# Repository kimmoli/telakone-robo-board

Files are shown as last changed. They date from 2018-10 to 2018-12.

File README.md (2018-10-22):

# telakone-robo-board

## Requirements

* Input power supply range 12..50V
* 5V regulator for external stuff (servos, LEDs, ...)
* CPU STM32F407
* RS-485 half-duplex serial interface
* PS2 (playstation) control (SPI)
  * SPI1
    * SPI1_SCK PB3 AF5
    * SPI1_MISO PB4 AF5
    * SPI1_MOSI PB5 AF5
    * SPI_CS_N PA8 OUTPUT
* I2C for external acceleration sensors
  * I2C1
    * I2C1_SCL PB6 AF4
    * I2C1_SDA PB7 AF4
* WS2812B control for LED lights
  * USART2
    * USART2_TX PA2
* USB device interface
  * Virtual serial port
    * OTG_FS_DM PA11 AF10
    * OTG_FS_DP PA12 AF10
	* USB_RENUM PB15 OUTPUT
* Wired UART
  * USART3
    * USART3_TX PD8 AF7
    * USART3_RX PD9 AF7
* RS485 UART
  * USART1
    * USART1_TX PA9 AF7
	* USART1_RX PA10 AF7
	* USART1_TXE PD15 OUTPUT
* Digital outputs
  * 1 enable output for stepper drivers
    * PE14 OUTPUT
  * 6 frequency outputs for stepper drivers
    * TIM4_CH1 PD12 AF2
    * TIM5_CH1 PA0 AF2
    * TIM8_CH1 PC6 AF3
    * TIM9_CH1 PE5 AF3
    * TIM10_CH1 PB8 AF3
    * TIM11_CH1 PB9 AF3
  * 6 direction outputs for stepper drivers
    * PE8 OUTPUT
    * PE9 OUTPUT
    * PE10 OUTPUT
    * PE11 OUTPUT
    * PE12 OUTPUT
    * PE13 OUTPUT
  * 2 servo signal outputs
    * TIM3_CH1 PA6 AF2
    * TIM3_CH2 PA7 AF2
  * 2 high side switch outputs
    * PC0 OUTPUT
    * PC1 OUTPUT
  * 3 debug led outputs
    * PC2 OUTPUT DEBUG (Green)
	* PC3 OUTPUT RUN (Green)
	* PC4 OUTPUT ERROR (Red)
* Digital inputs
  * 16 inputs for limit/zero switches, emergency stop
    * PC8 INPUT
    * PC9 INPUT
    * PC10 INPUT
    * PC11 INPUT
    * PC12 INPUT
    * PC13 INPUT
    * PC14 INPUT
    * PC15 INPUT
    * PD0 INPUT
    * PD1 INPUT
    * PD2 INPUT
    * PD3 INPUT
    * PD4 INPUT
    * PD5 INPUT
    * PD6 INPUT
    * PD7 INPUT

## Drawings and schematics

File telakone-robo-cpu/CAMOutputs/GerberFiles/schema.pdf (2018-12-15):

+5V 3A

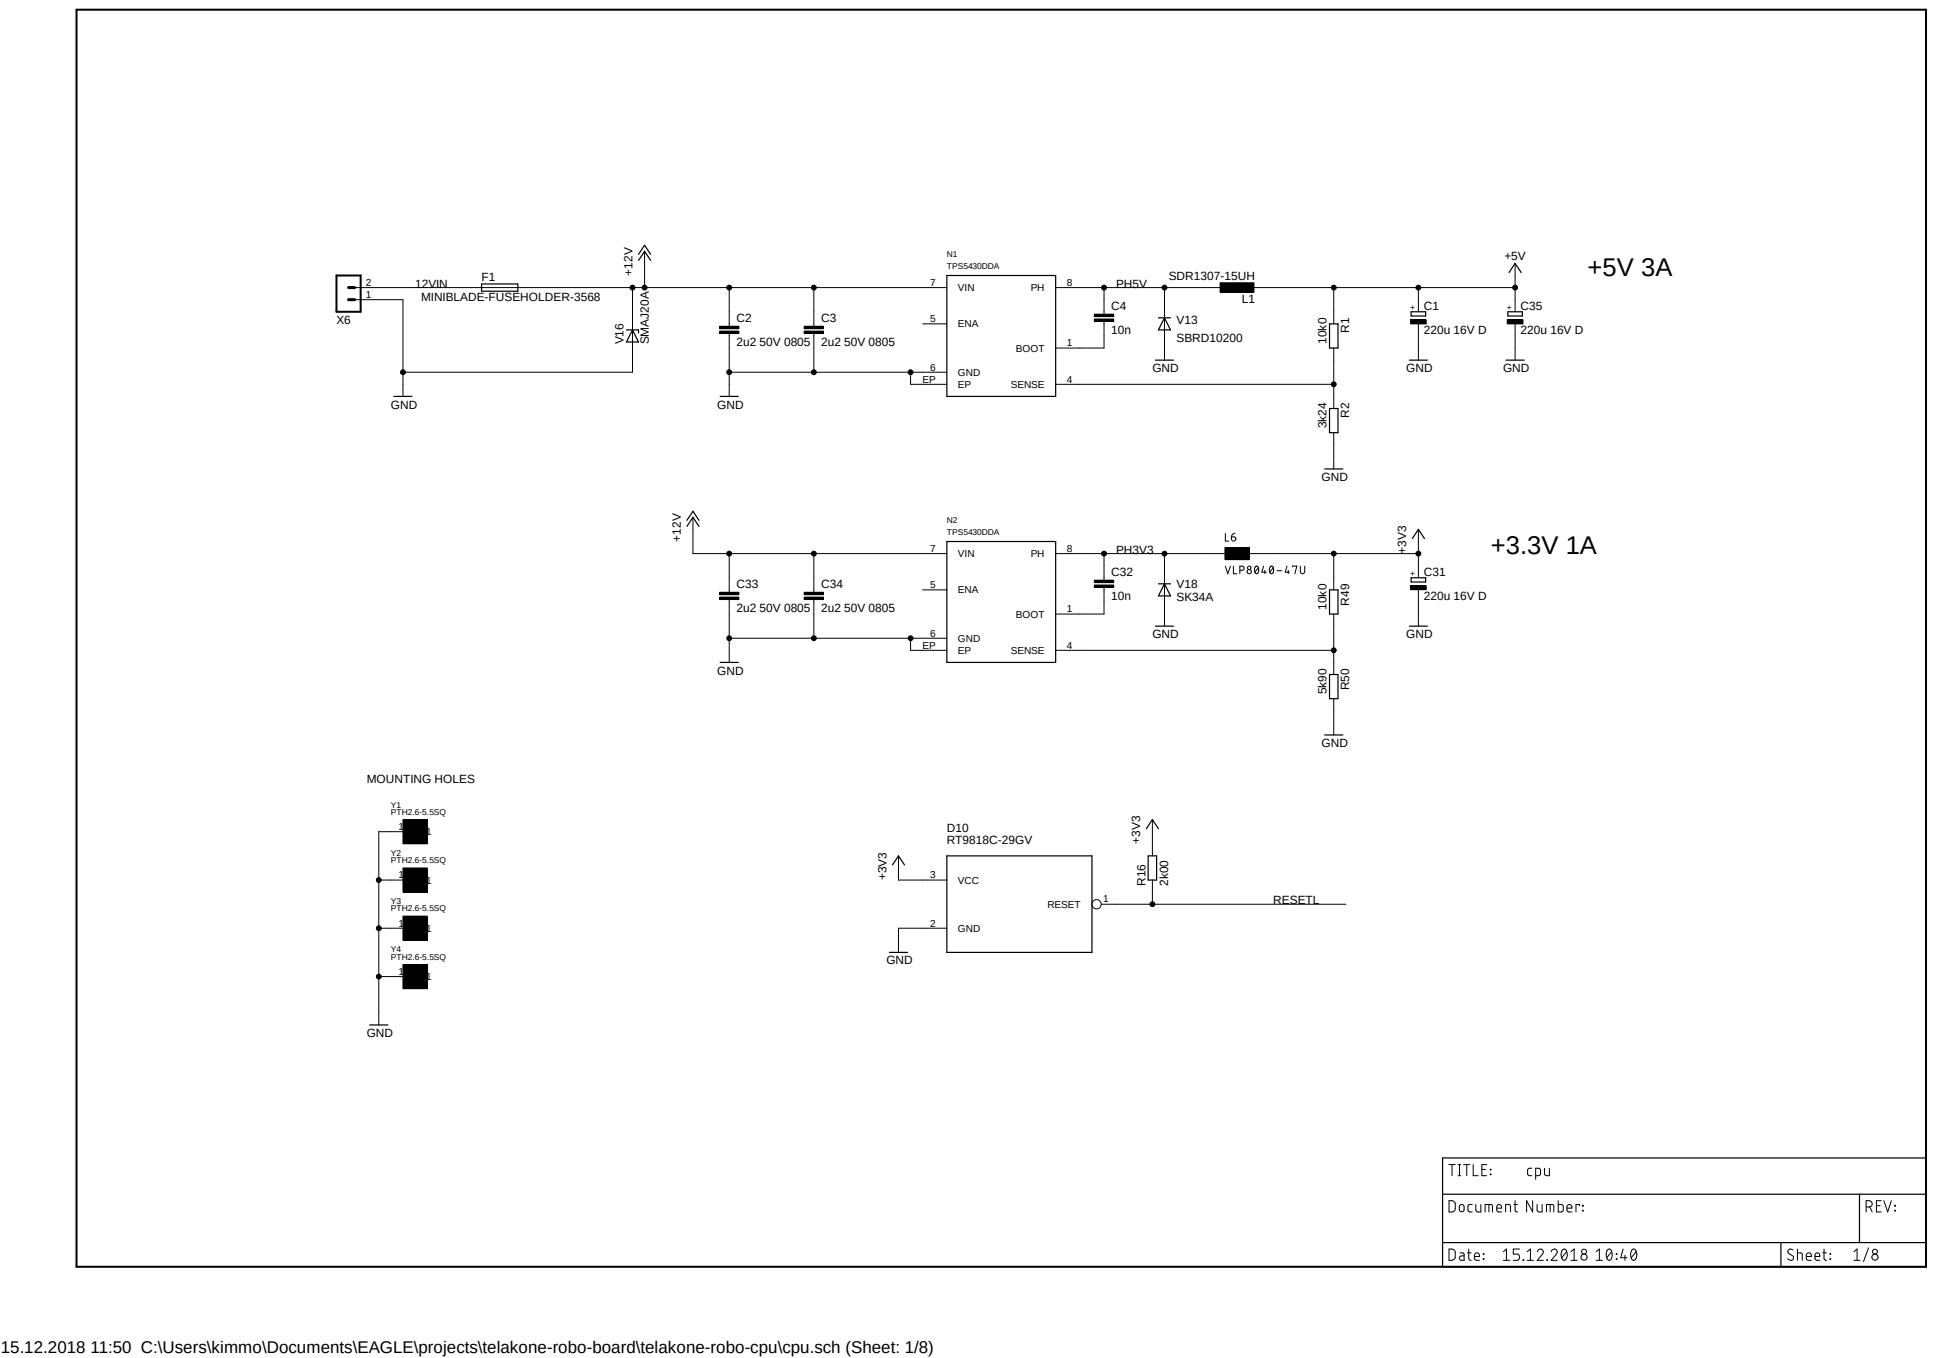
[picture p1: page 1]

15.12.2018 11:50 C:\Users\kimmo\Documents\EAGLE\projects\telakone-robo-board\telakone-robo-cpu\cpu.sch (Sheet: 1/8)

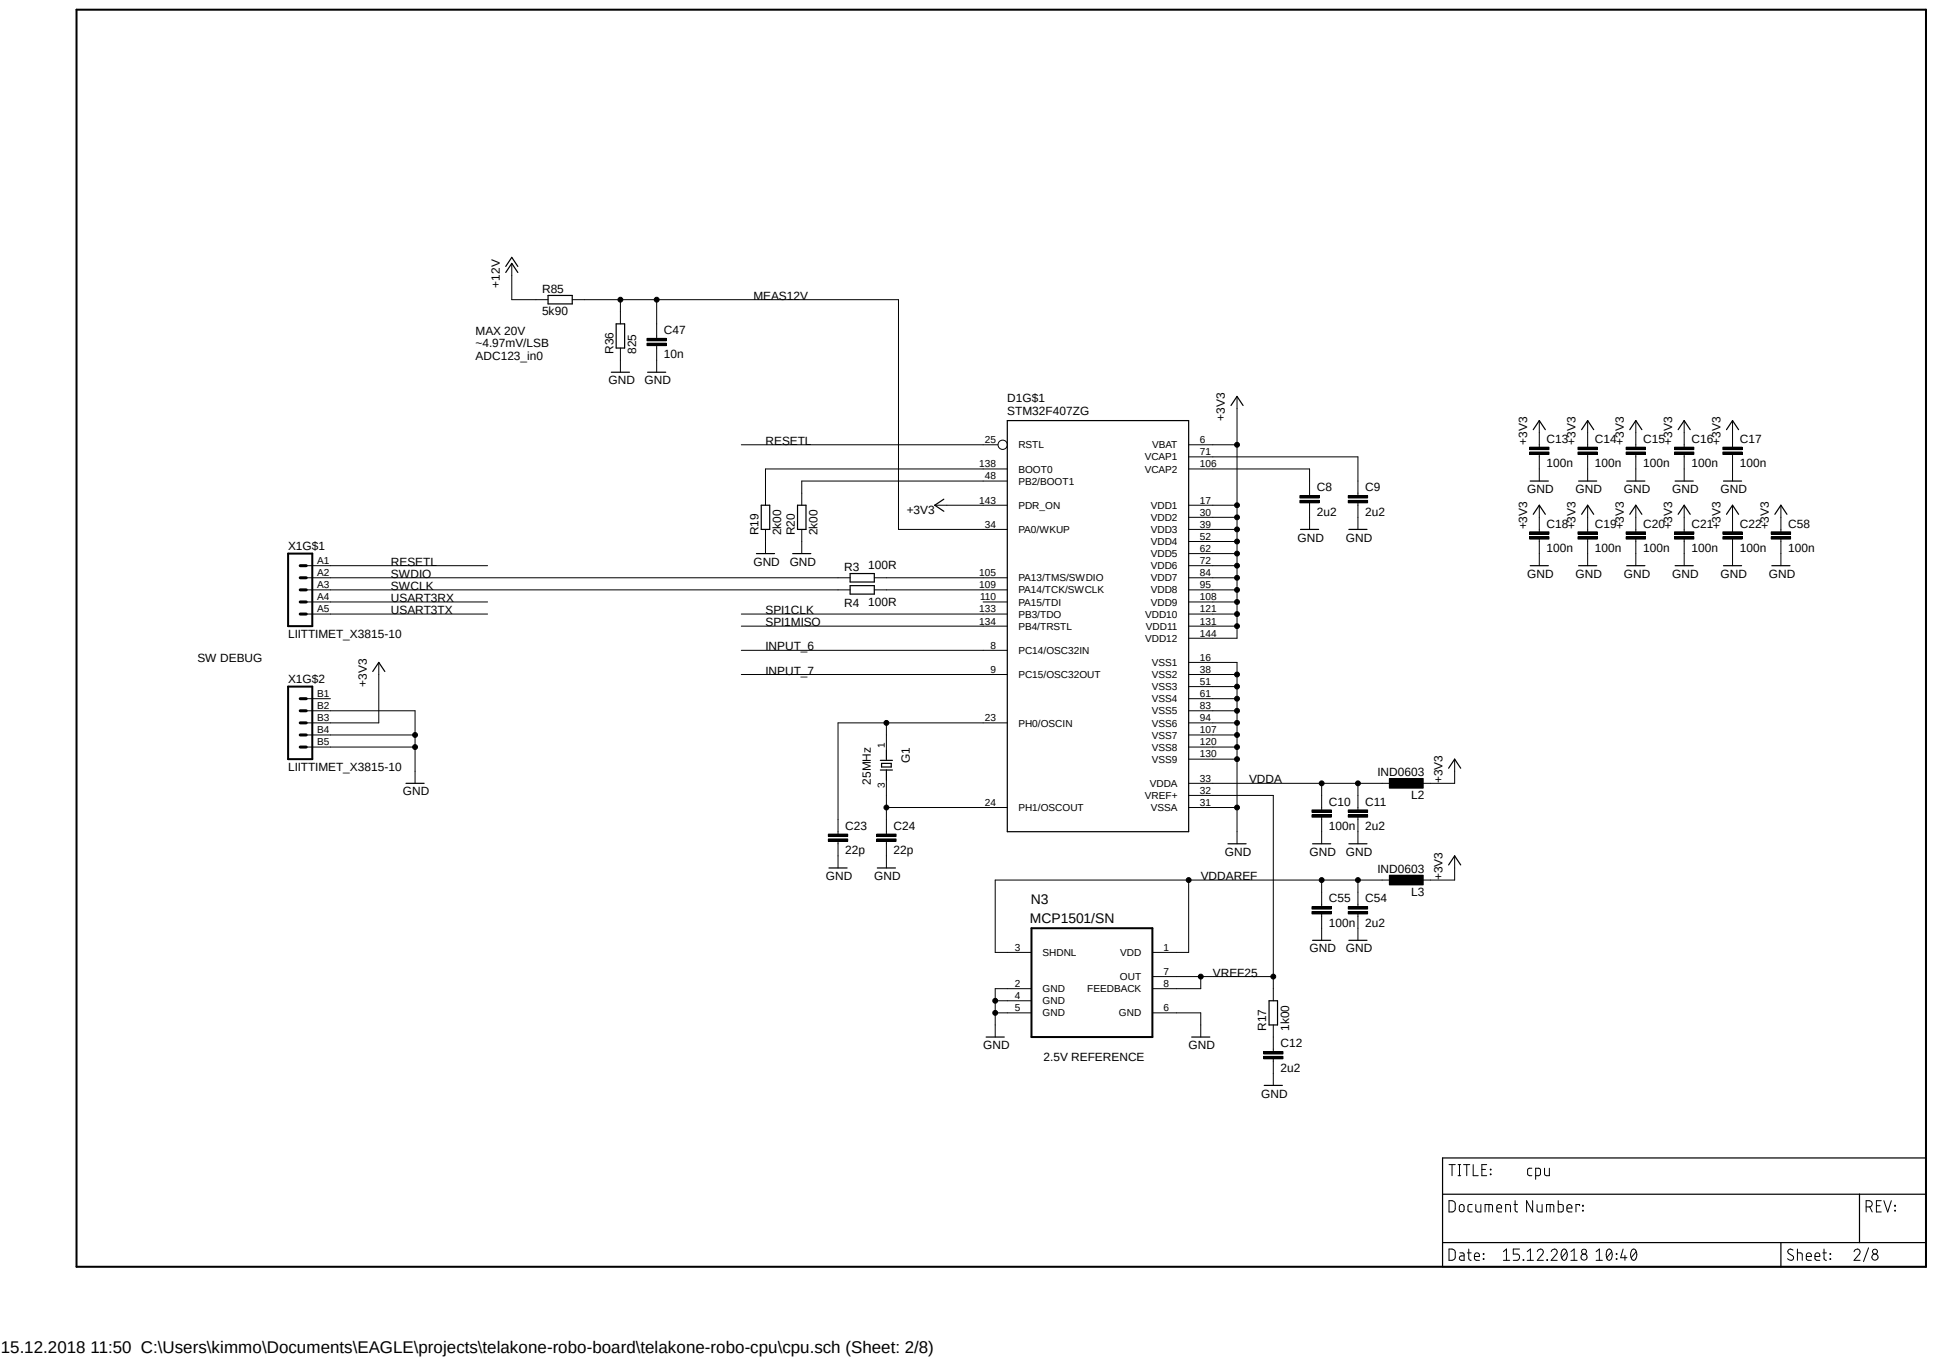
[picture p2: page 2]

15.12.2018 11:50 C:\Users\kimmo\Documents\EAGLE\projects\telakone-robo-board\telakone-robo-cpu\cpu.sch (Sheet: 2/8)

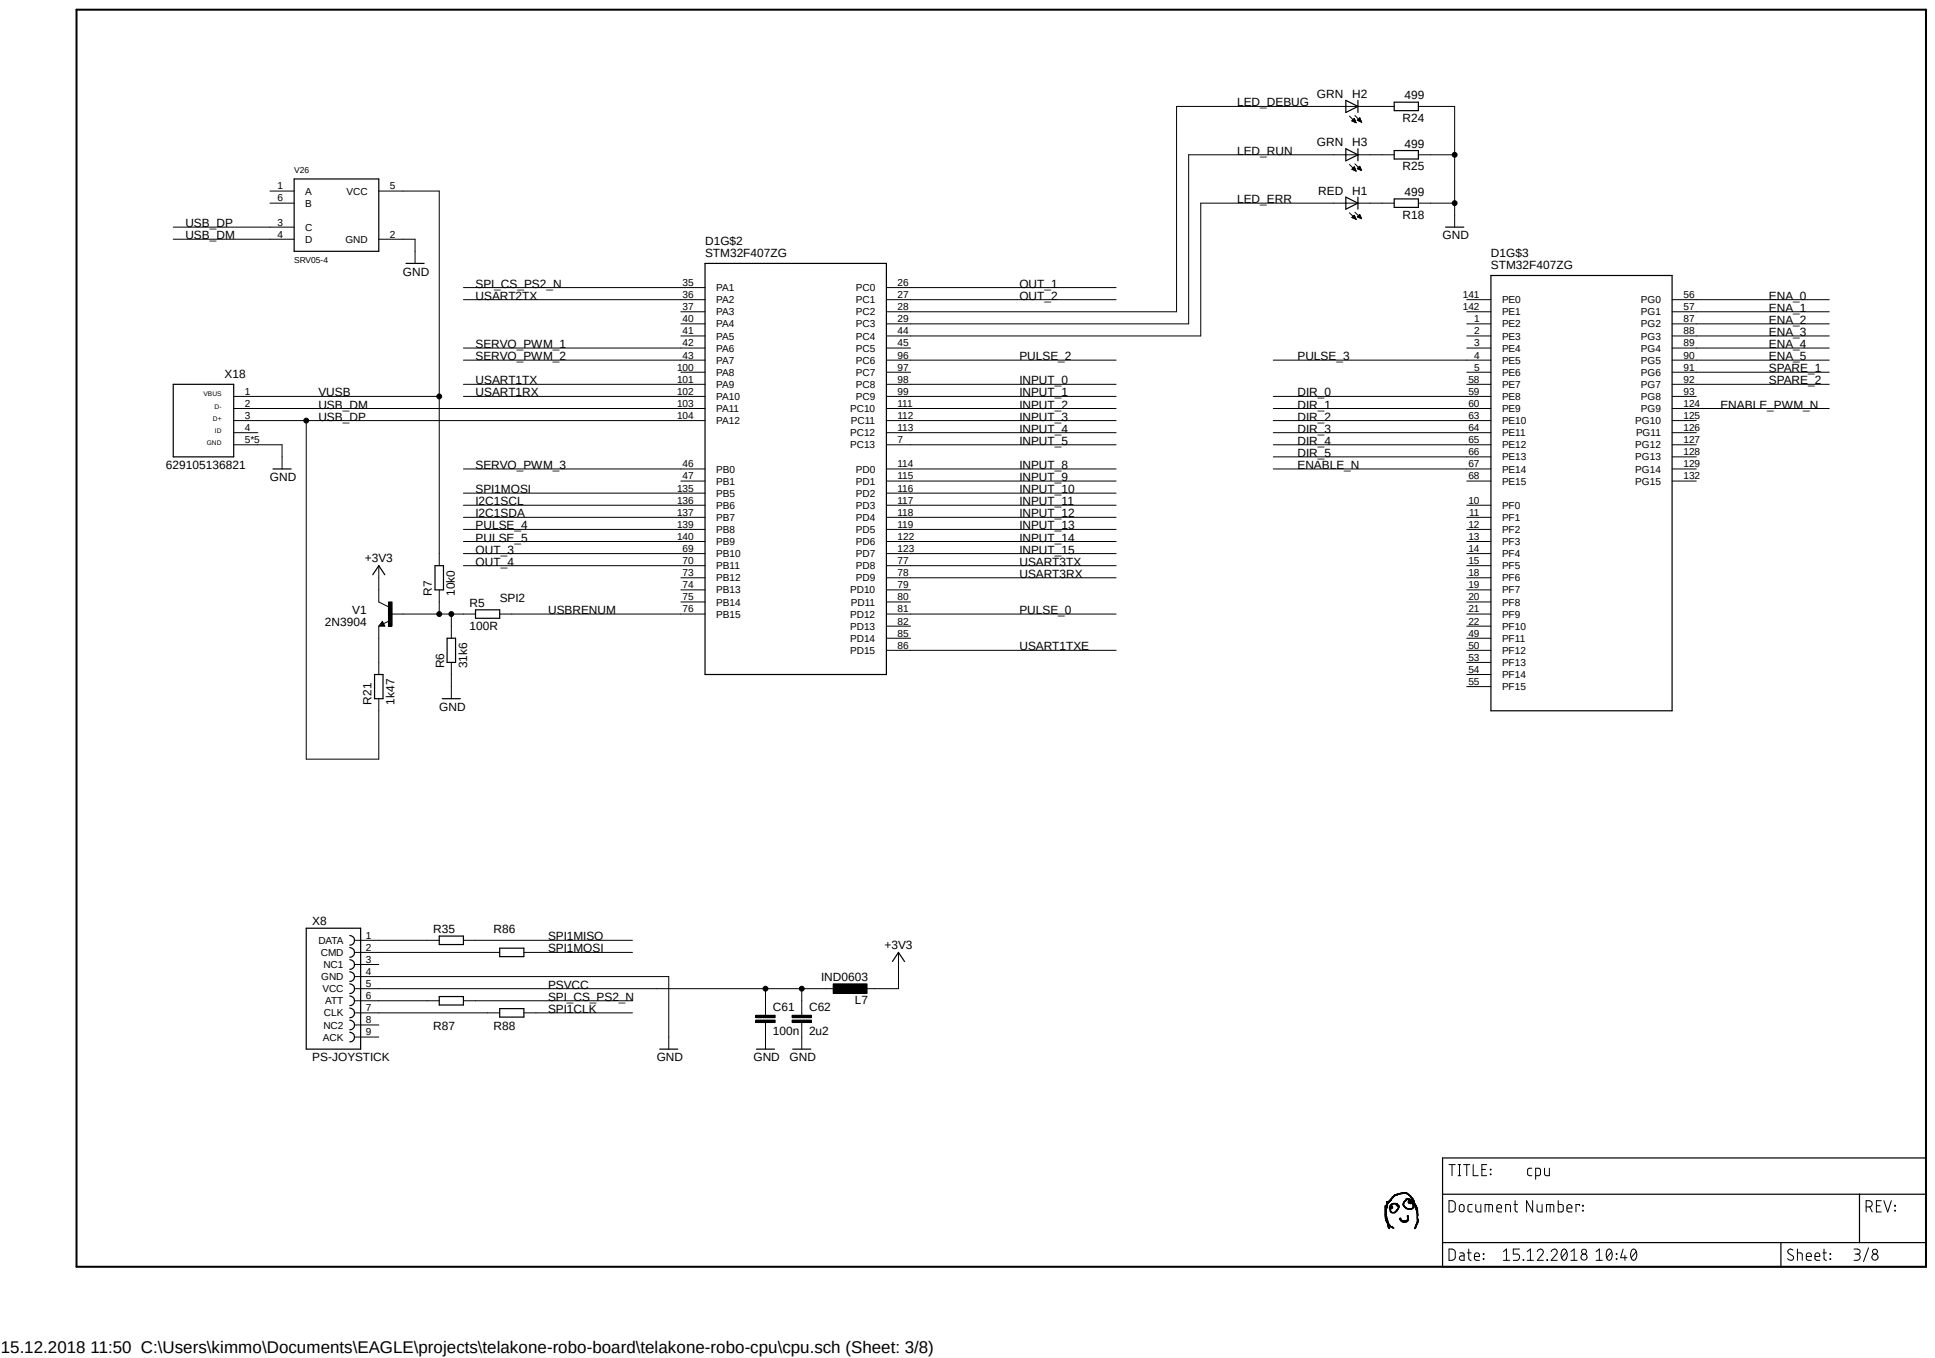
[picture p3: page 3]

2 USB_DM | PA11 103
3 USB_DP | PA12 104
4 5*5 | SERVO_PWM_3 | PB0 46

15.12.2018 11:50 C:\Users\kimmo\Documents\EAGLE\projects\telakone-robo-board\telakone-robo-cpu\cpu.sch (Sheet: 3/8)

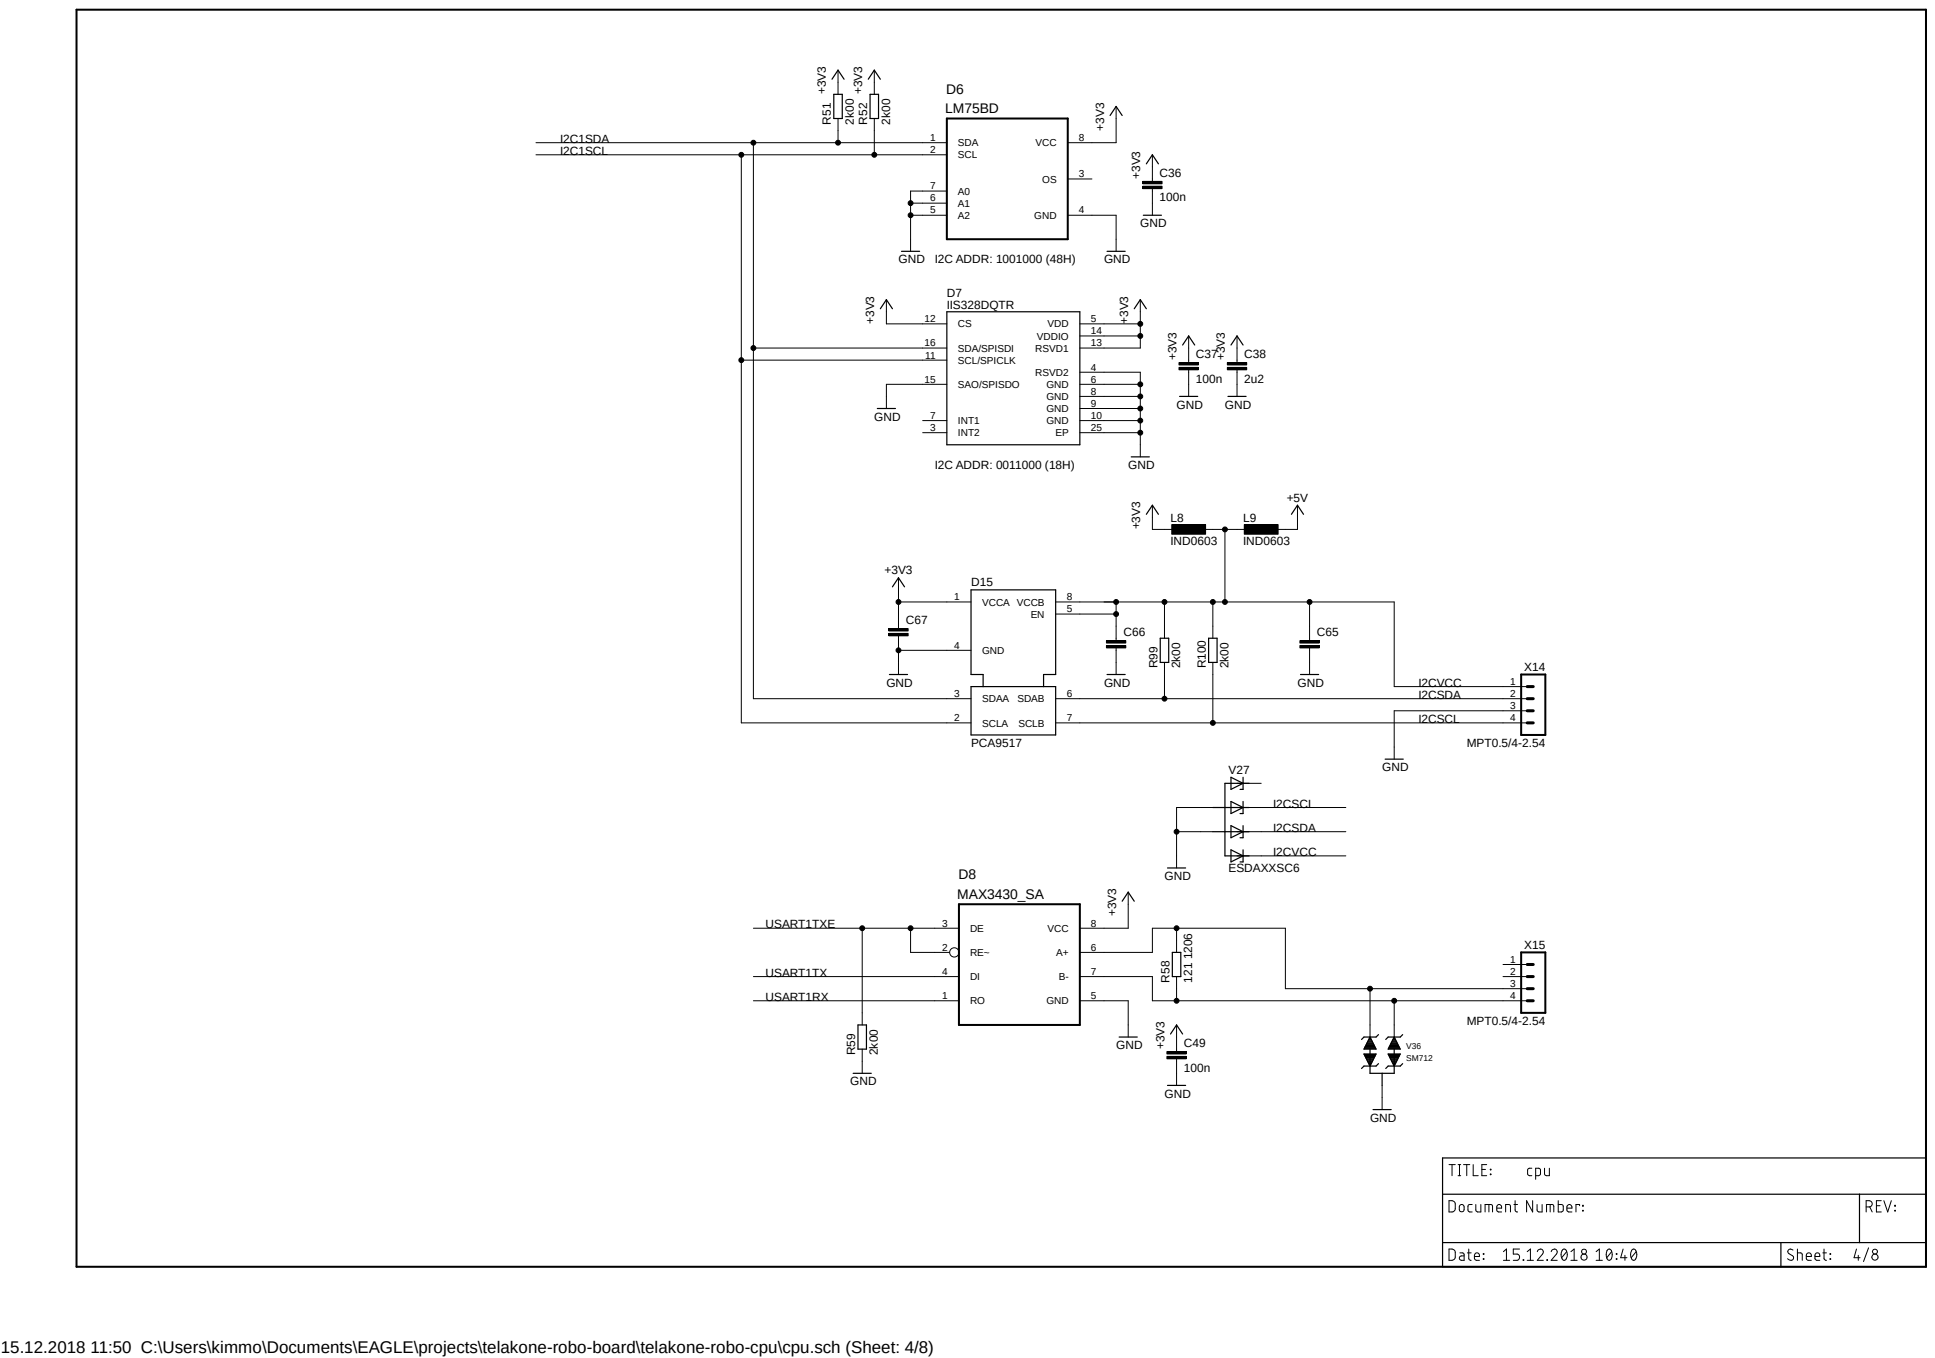
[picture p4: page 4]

15.12.2018 11:50 C:\Users\kimmo\Documents\EAGLE\projects\telakone-robo-board\telakone-robo-cpu\cpu.sch (Sheet: 4/8)

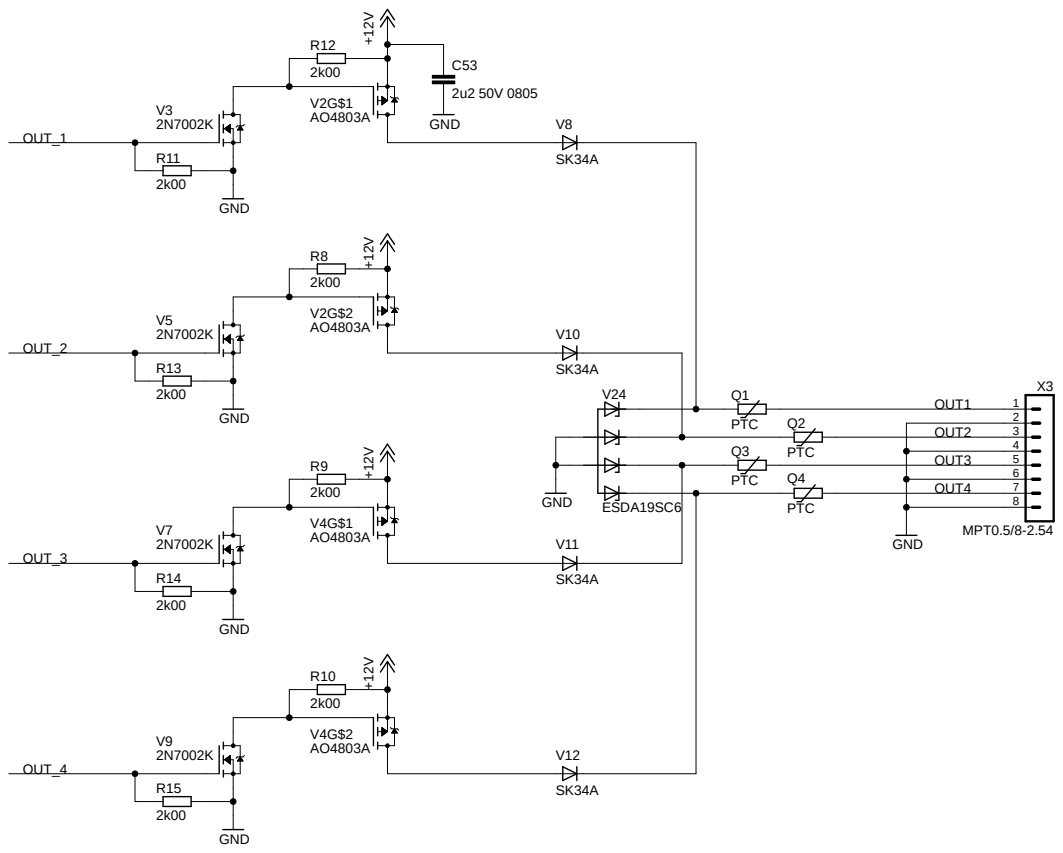
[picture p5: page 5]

15.12.2018 11:50 C:\Users\kimmo\Documents\EAGLE\projects\telakone-robo-board\telakone-robo-cpu\cpu.sch (Sheet: 5/8)

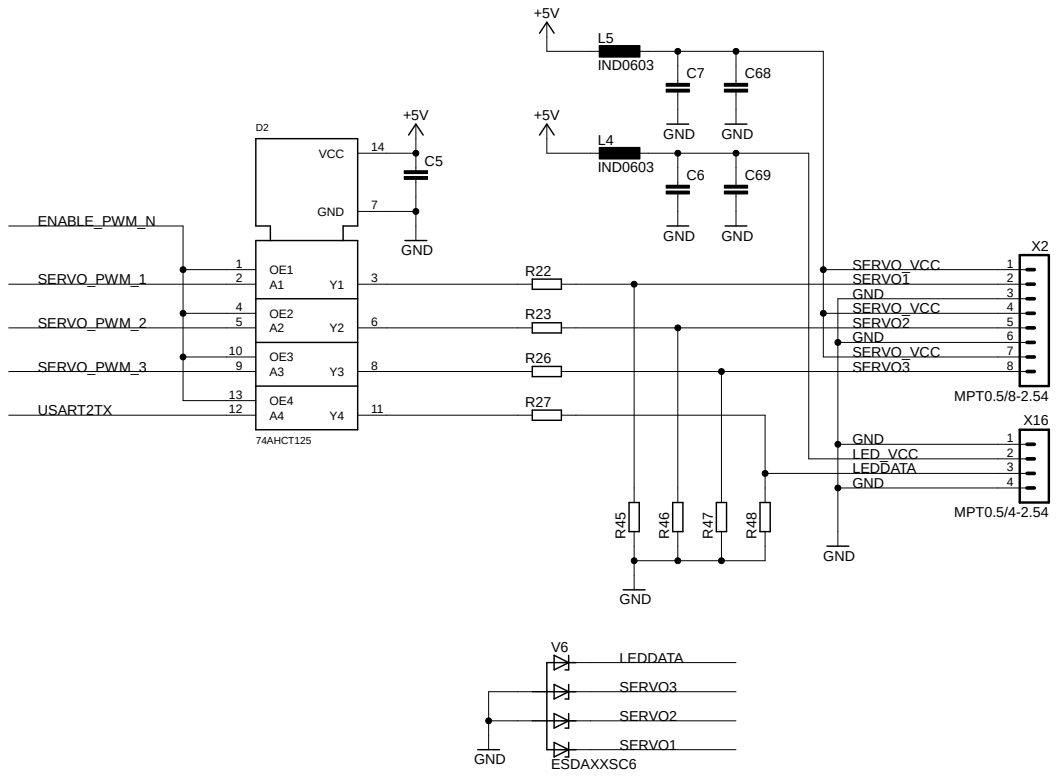
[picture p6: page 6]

15.12.2018 11:50 C:\Users\kimmo\Documents\EAGLE\projects\telakone-robo-board\telakone-robo-cpu\cpu.sch (Sheet: 6/8)

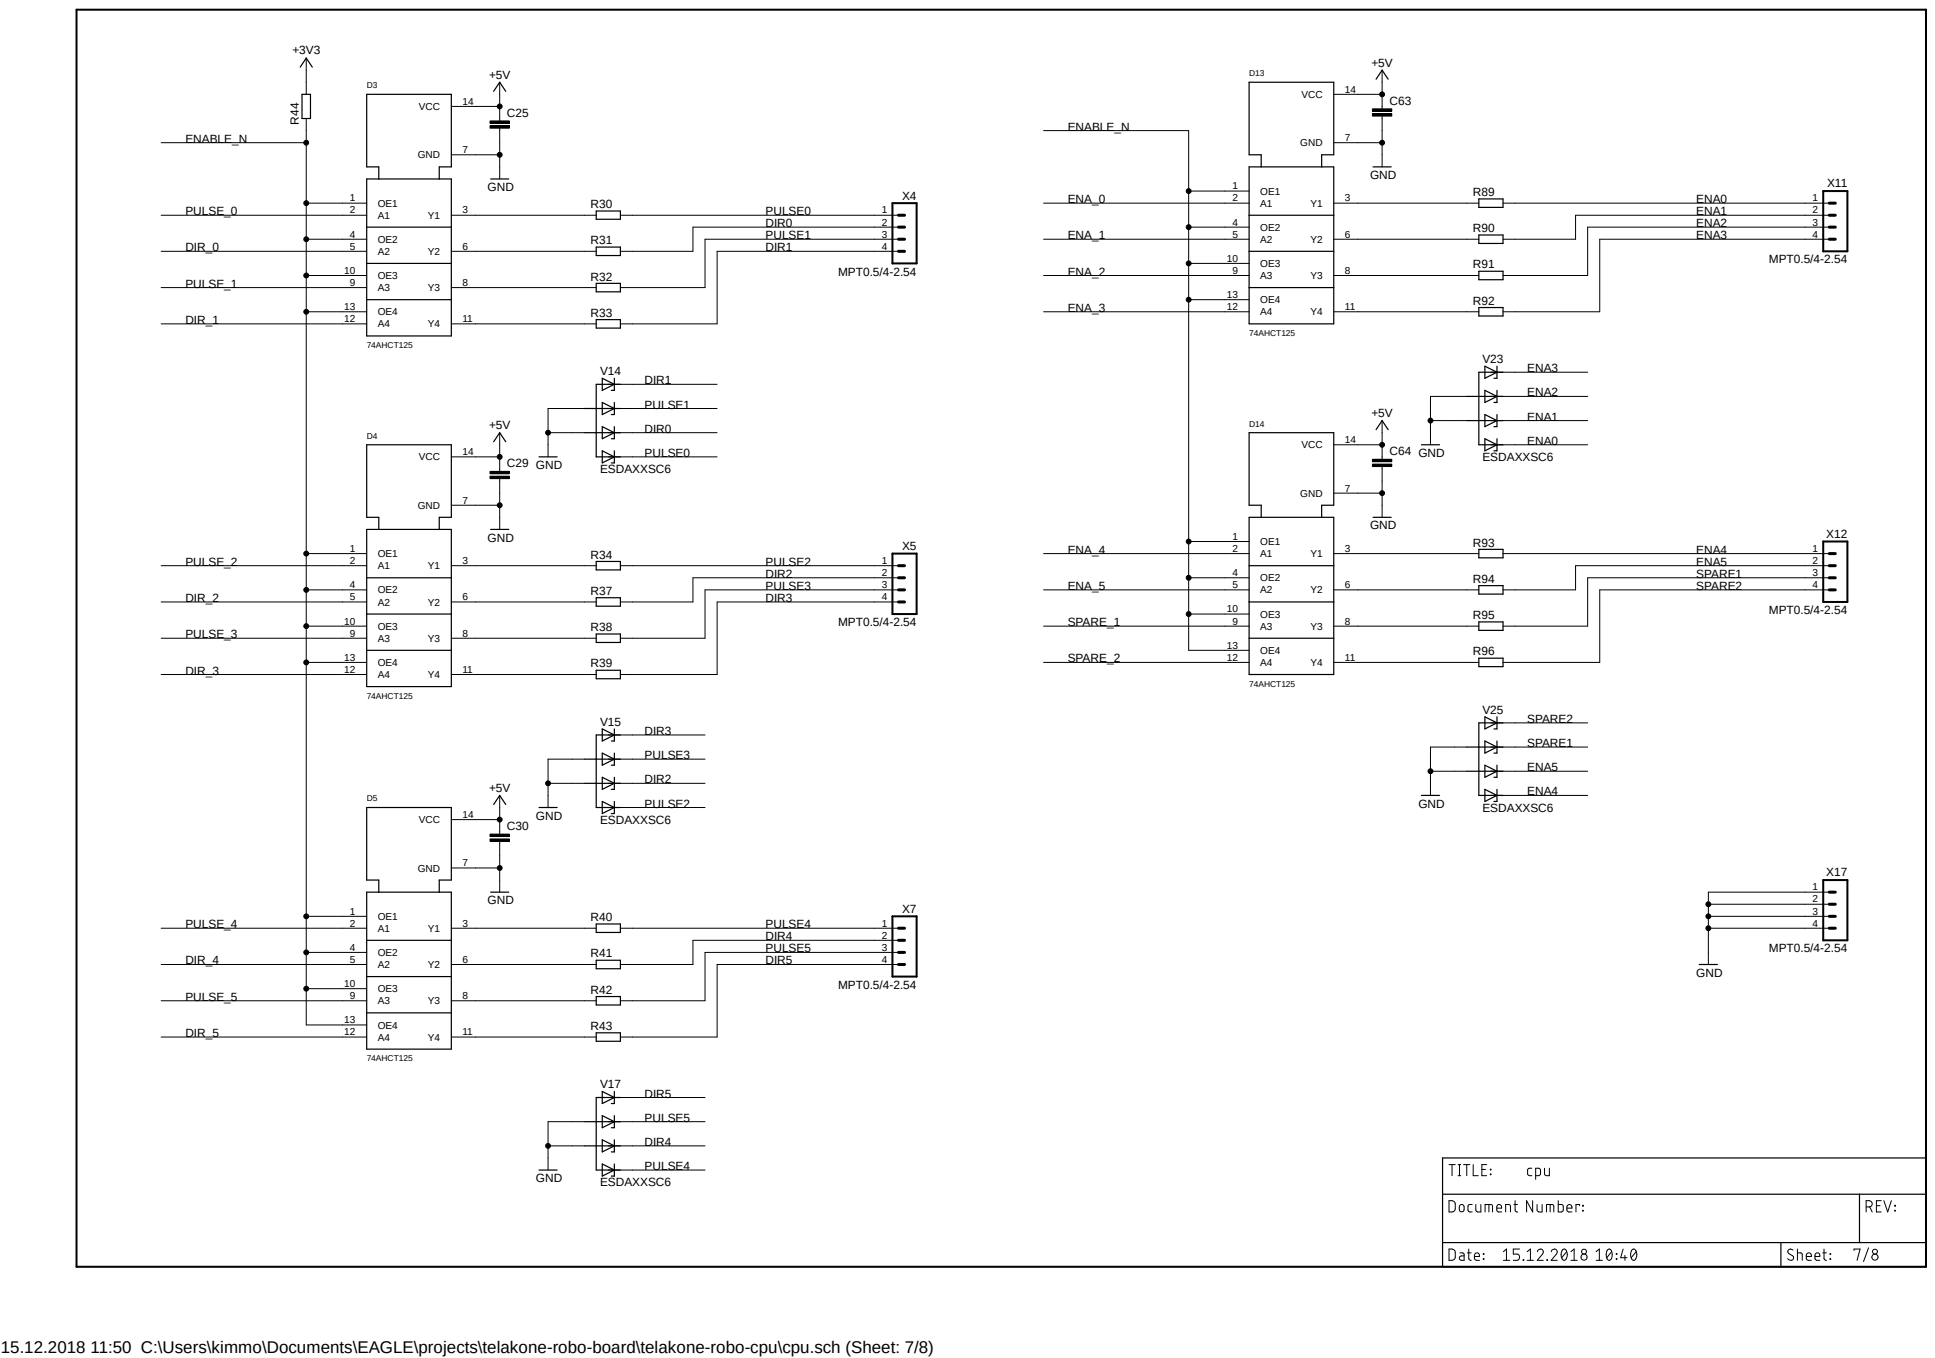
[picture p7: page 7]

15.12.2018 11:50 C:\Users\kimmo\Documents\EAGLE\projects\telakone-robo-board\telakone-robo-cpu\cpu.sch (Sheet: 7/8)

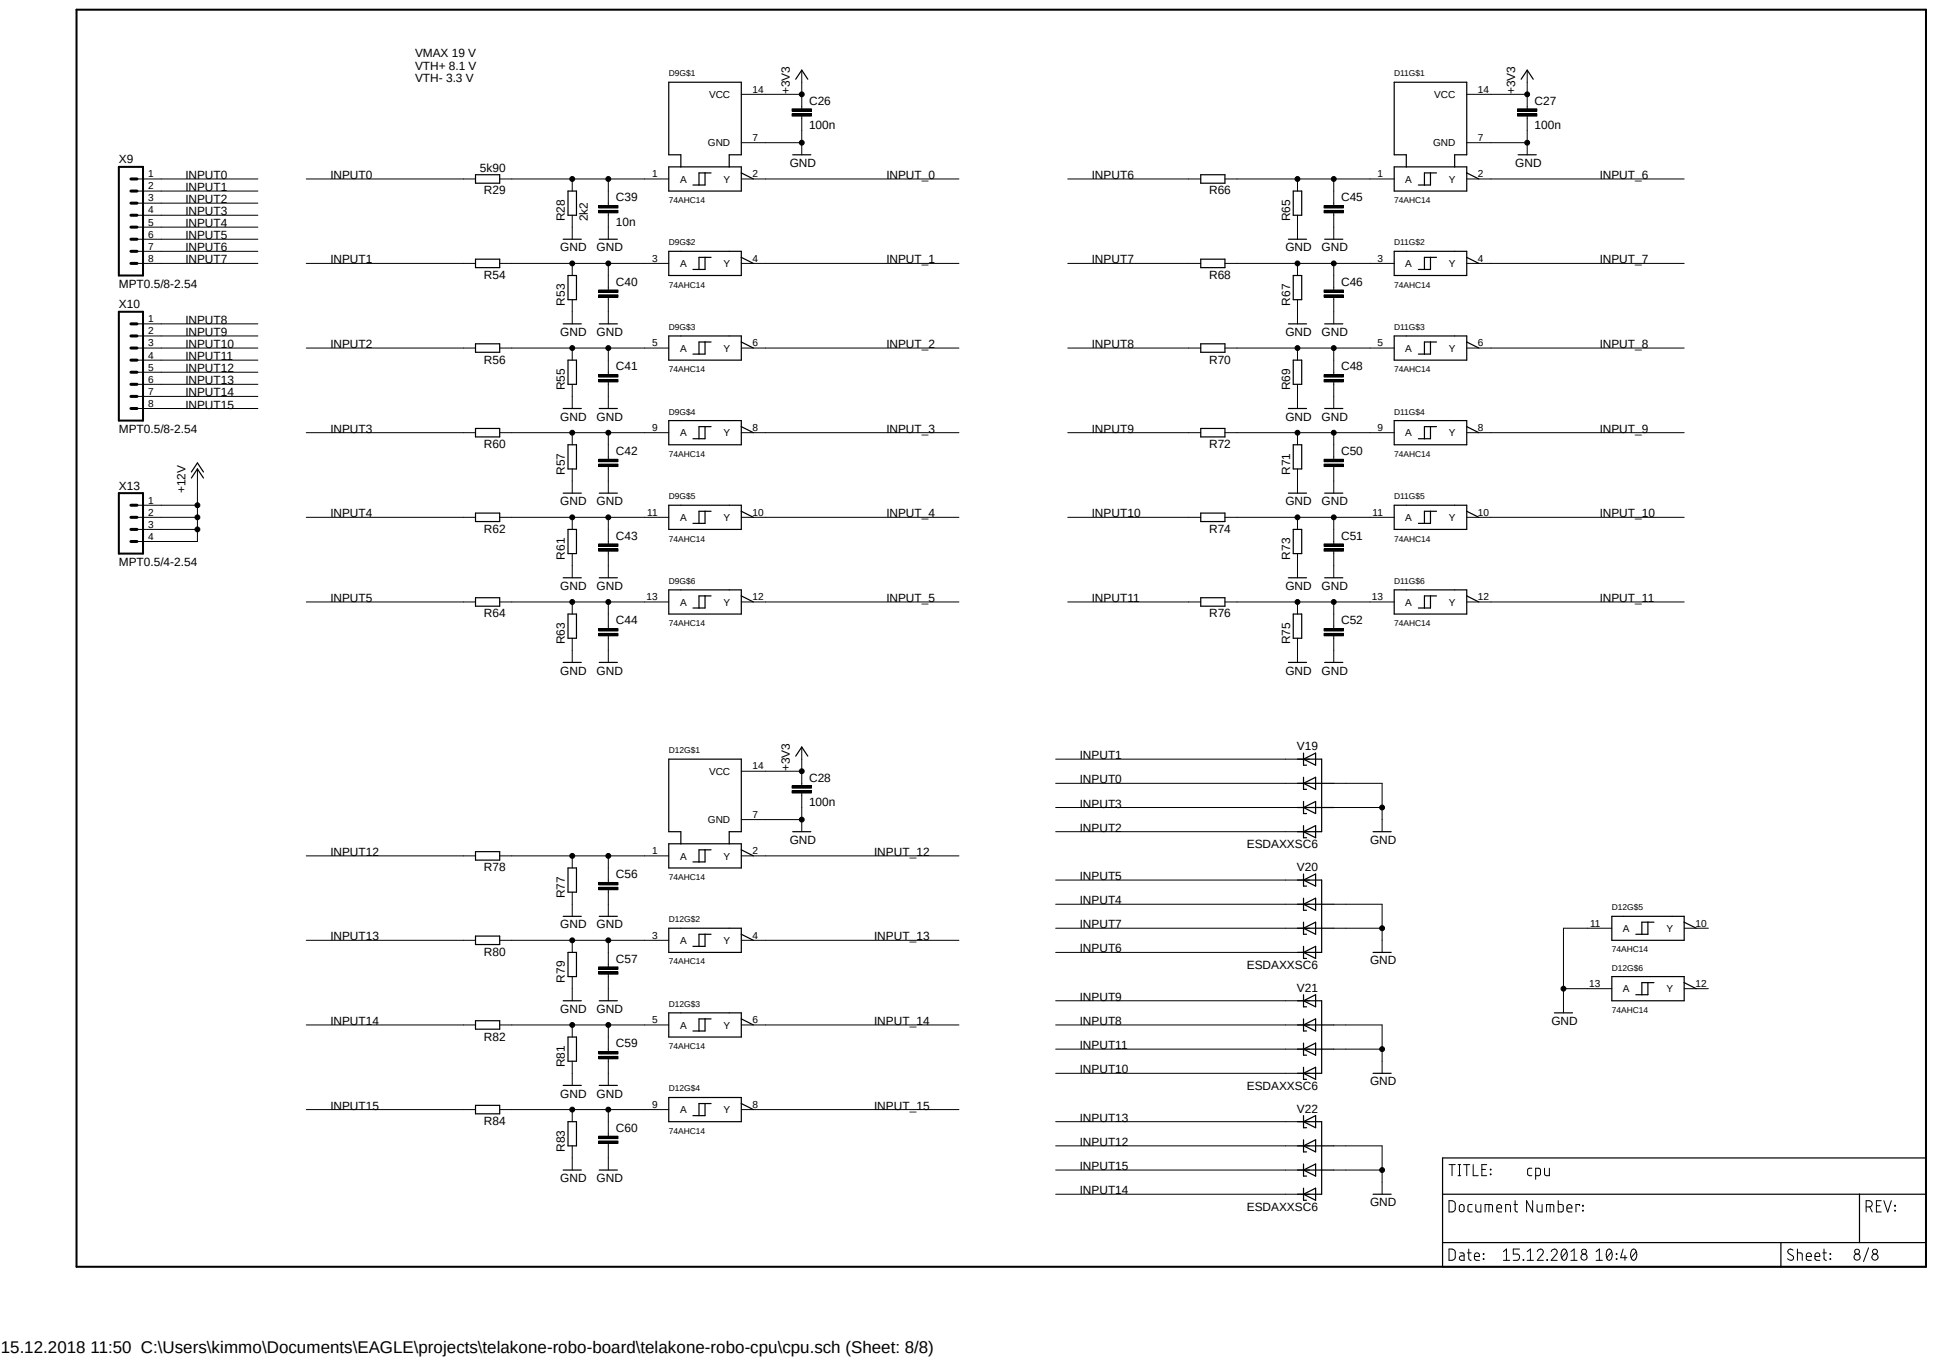
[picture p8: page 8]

15.12.2018 11:50 C:\Users\kimmo\Documents\EAGLE\projects\telakone-robo-board\telakone-robo-cpu\cpu.sch (Sheet: 8/8)

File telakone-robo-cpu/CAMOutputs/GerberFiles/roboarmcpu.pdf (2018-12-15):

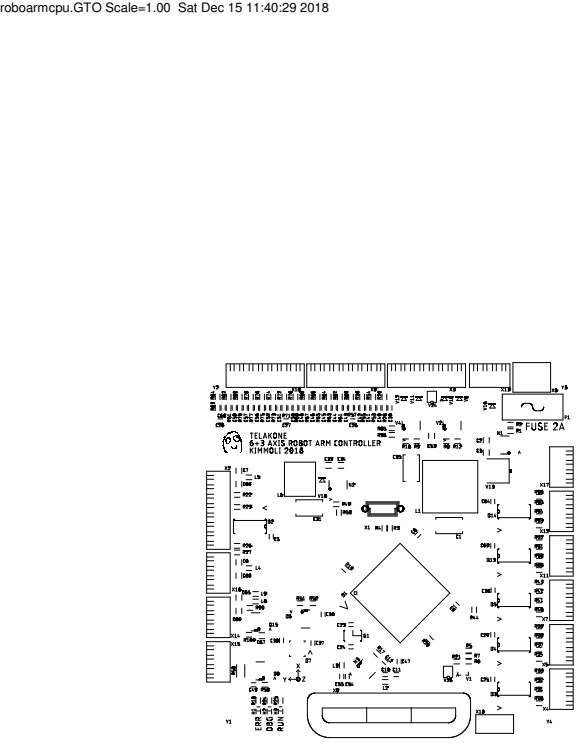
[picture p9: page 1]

roboarmcpu.GTO Scale=1.00 Sat Dec 15 11:40:29 2018

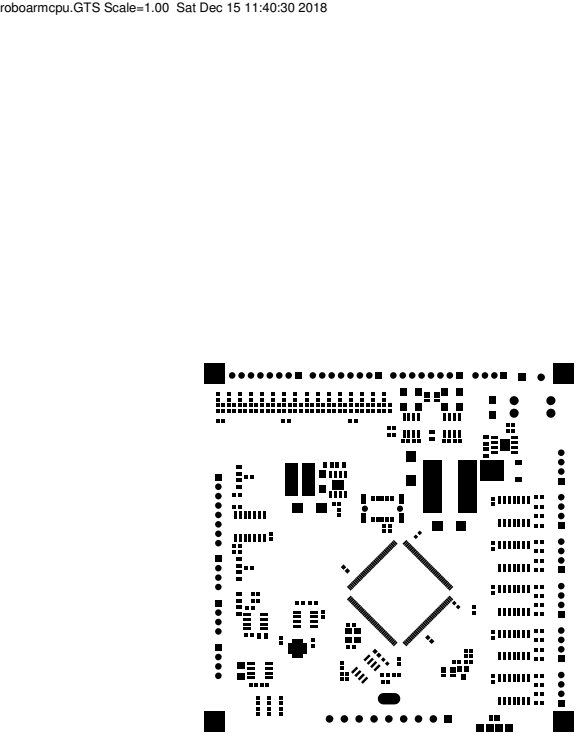
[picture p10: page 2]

roboarmcpu.GTS Scale=1.00 Sat Dec 15 11:40:30 2018

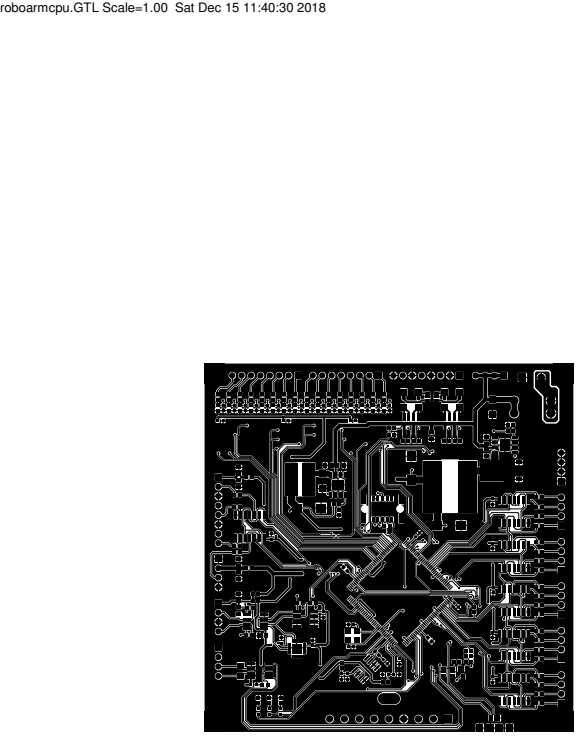
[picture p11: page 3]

roboarmcpu.GTL Scale=1.00 Sat Dec 15 11:40:30 2018

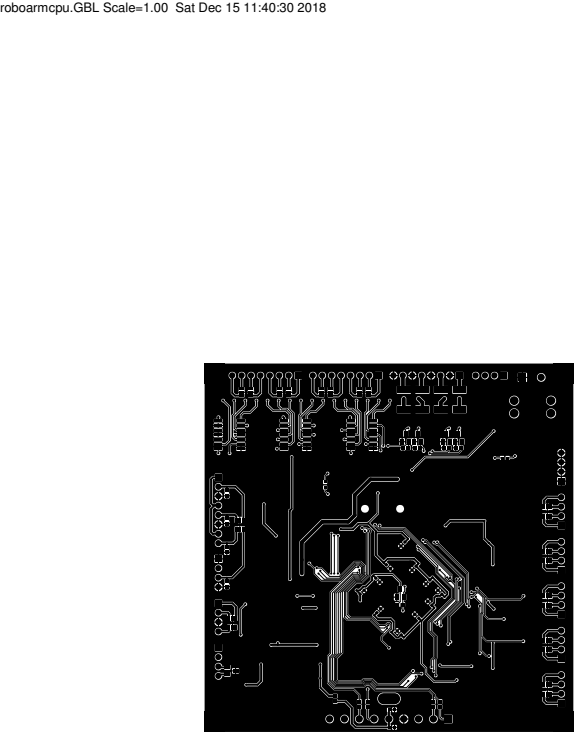
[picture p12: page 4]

roboarmcpu.GBL Scale=1.00 Sat Dec 15 11:40:30 2018


roboarmcpu.GBS Scale=1.00 Sat Dec 15 11:40:30 2018


roboarmcpu.GBO Scale=1.00 Sat Dec 15 11:40:30 2018

roboarmcpu.GKO Scale=1.00 Sat Dec 15 11:40:30 2018


roboarmcpu.TXT Scale=1.00 Sat Dec 15 11:40:30 2018

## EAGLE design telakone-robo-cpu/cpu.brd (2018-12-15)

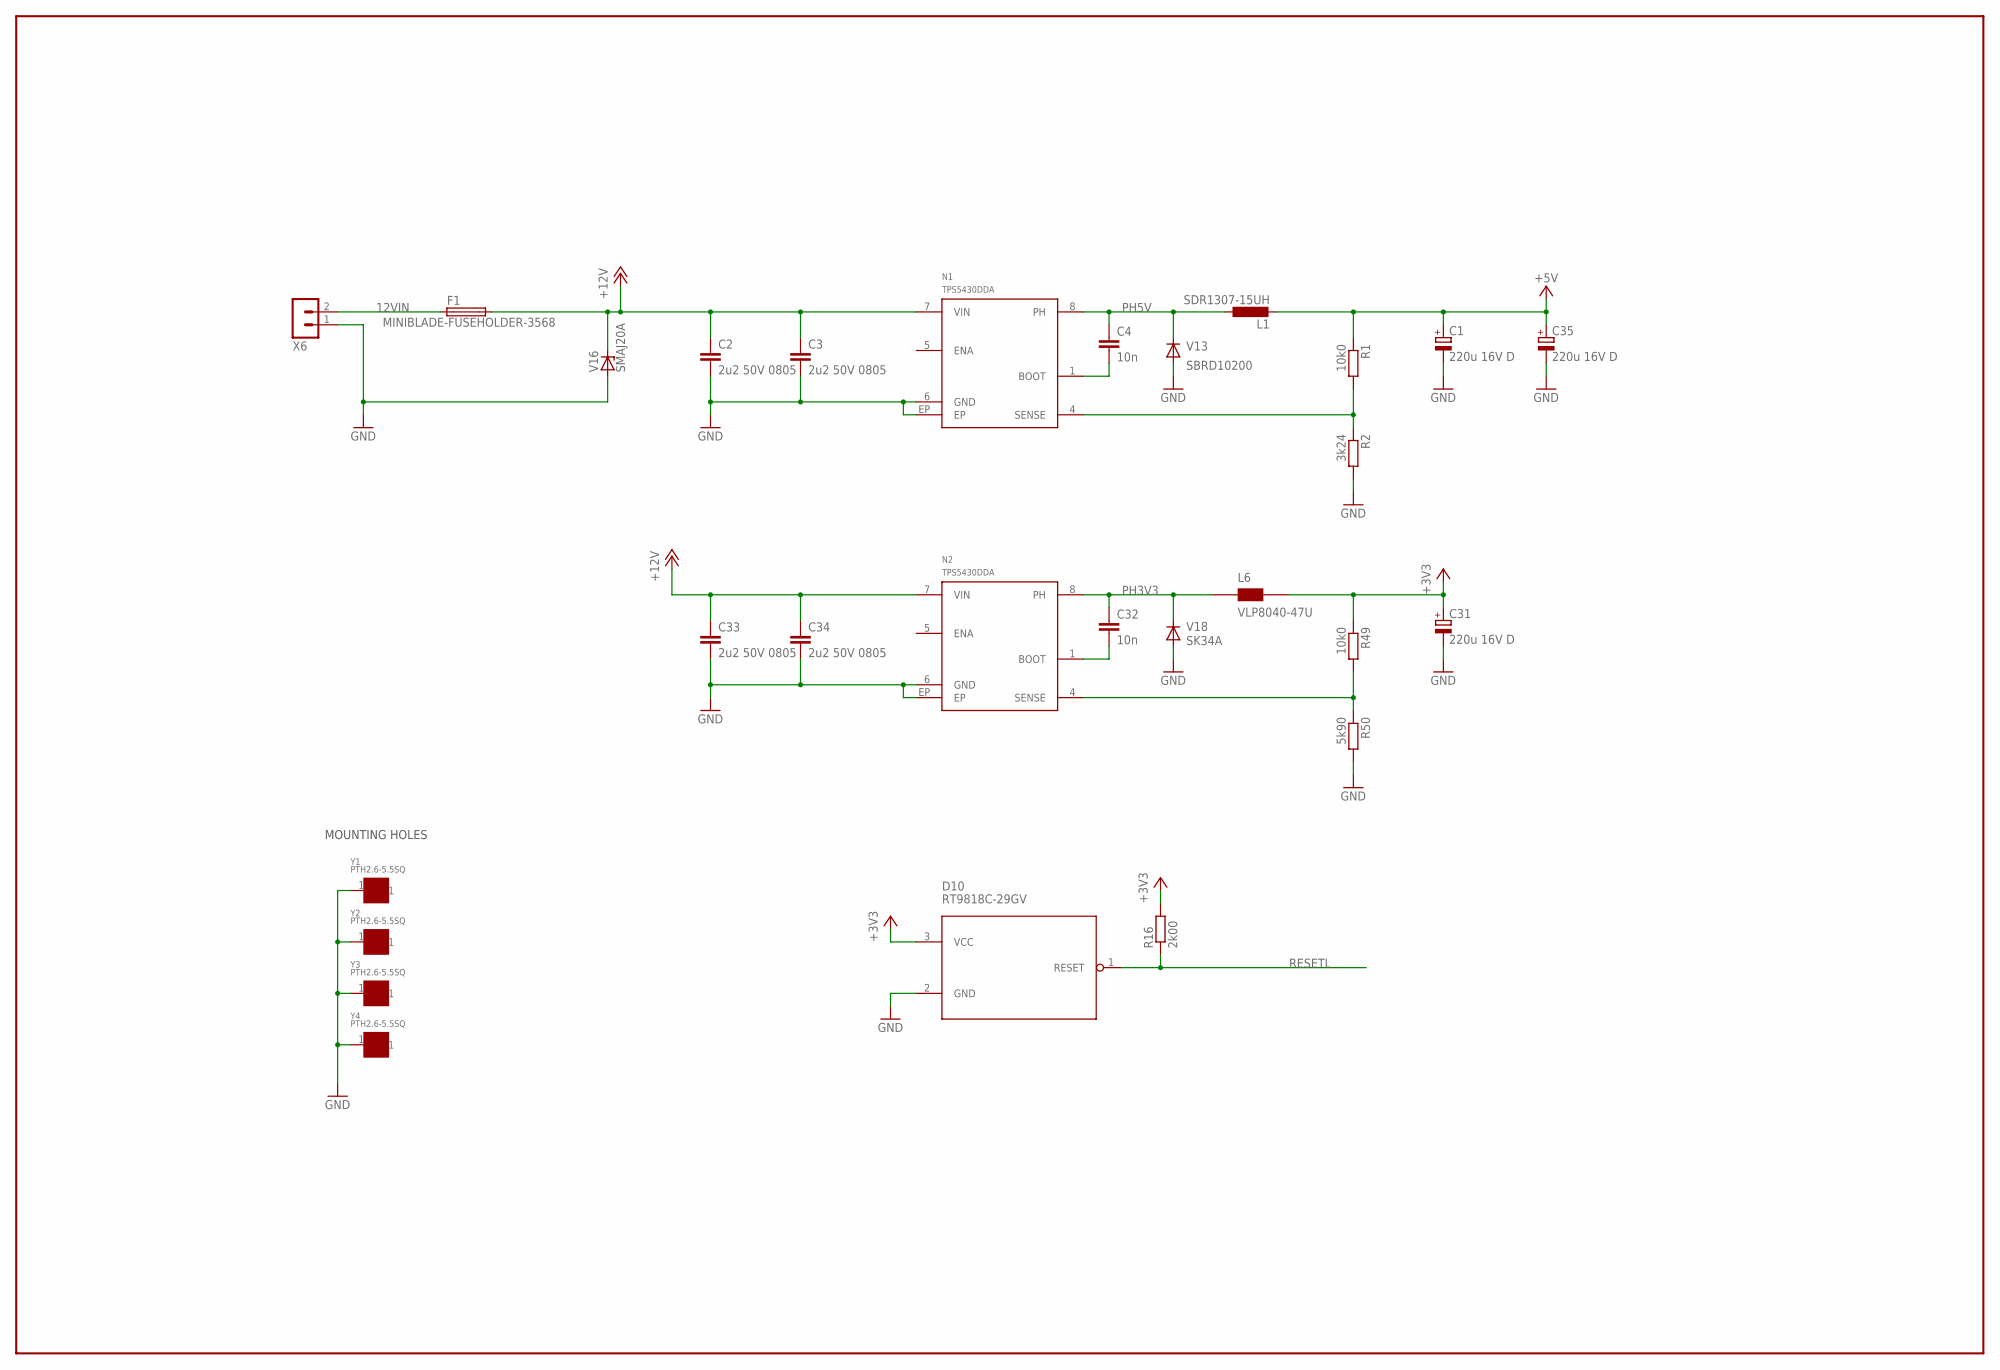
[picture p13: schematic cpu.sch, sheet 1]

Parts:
C1, C31, C35: 220u 16V D; CT7343
C2, C3, C33, C34: 2u2 50V 0805; C0805
C4, C32: 10n; C0603
D10: RT9818C-29GV; SOT23
F1: MINIBLADE-FUSEHOLDER-3568; KEYSTONE-3568
L1: SDR1307-15UH; SDR1307
L6: VLP8040-47U; VLP8040
N1, N2: TPS5430DDA; SOIC8-N-EP
R1, R49: 10k0; R0603
R2: 3k24; R0603
R16: 2k00; R0603
R50: 5k90; R0603
V13: SBRD10200; DPACK
V16: SMAJ20A; DO214AC
V18: SK34A; DO214AC
X6: TE_RUUVILIITIN2
Y1, Y2, Y3, Y4: PTH2.6-5.5SQ; PTH-2.6-5.5SQ

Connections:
12VIN: F1.1, F1.4 (1), X6.2
+3V3: C31.+, D10.3 (VCC), L6.2 (B), R16.2, R49.1; also elsewhere on the board
+5V: C1.+, C35.+, L1.2, R1.1; also elsewhere on the board
+12V: C2.1, C3.1, C33.1, C34.1, F1.2, F1.3 (2), N1.7 (VIN), N2.7 (VIN), V16.C; also elsewhere on the board
BOOT3V3: C32.2, N2.1 (BOOT)
BOOT5V: C4.2, N1.1 (BOOT)
GND: C1.-, C2.2, C3.2, C31.-, C33.2, C34.2, C35.-, D10.2 (GND), N1.6 (GND), N1.EP, N2.6 (GND), N2.EP, R2.2, R50.2, V13.1 (A), V13.3 (A), V16.A, V18.A, X6.1, Y1.1, Y2.1, Y3.1, Y4.1; also elsewhere on the board
unnamed: N1.4 (SENSE), R1.2, R2.1
unnamed: N2.4 (SENSE), R49.2, R50.1
PH3V3: C32.1, L6.1 (A), N2.8 (PH), V18.C
PH5V: C4.1, L1.1, N1.8 (PH), V13.2 (C)
RESETL: D10.1 (RESET), R16.1; also elsewhere on the board

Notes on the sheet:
MOUNTING HOLES

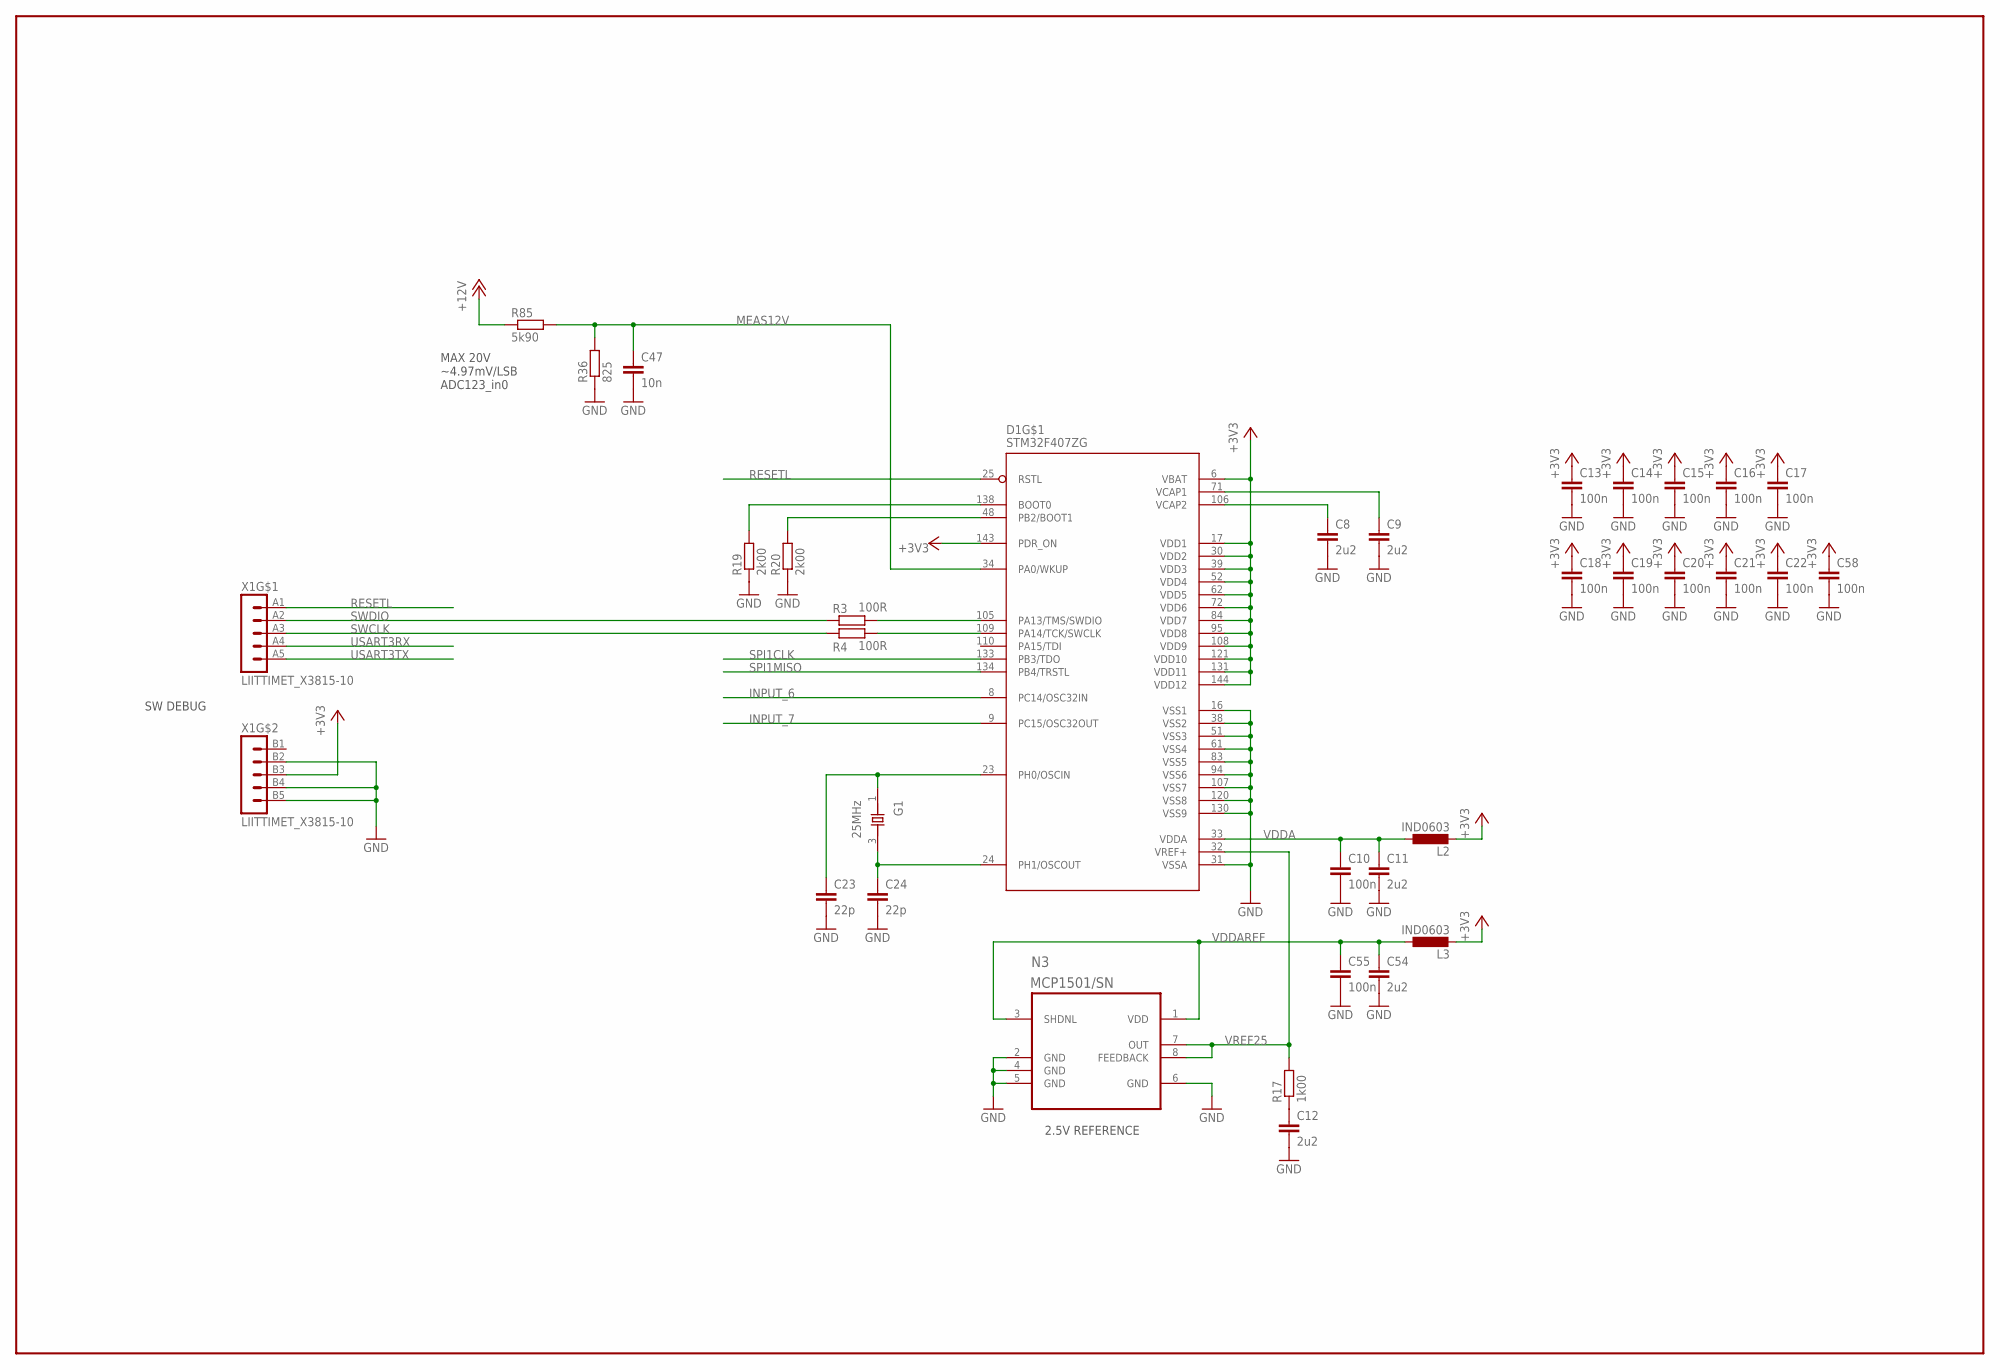
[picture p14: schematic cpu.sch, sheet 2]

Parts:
C8, C9, C11, C12, C54: 2u2; C0603
C10, C13, C14, C15, C16, C17, C18, C19, C20, C21, C22, C55, C58: 100n; C0603
C23, C24: 22p; C0603
C47: 10n; C0603
D1: STM32F407ZG; LQFP-144
G1: 25MHz; X_3225
L2, L3: IND0603; R0603
N3: MCP1501/SN; SOIC8-N_MC
R3, R4: 100R; PASSIIVIT_R0603
R17: 1k00; R0603
R19, R20: 2k00; R0603
R36: 825; R0603
R85: 5k90; R0603
X1: LIITTIMET_X3815-10; LIITTIMET_15110102601

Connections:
+3V3: C13.1, C14.1, C15.1, C16.1, C17.1, C18.1, C19.1, C20.1, C21.1, C22.1, C58.1, D1.6 (VBAT), D1.17 (VDD1), D1.30 (VDD2), D1.39 (VDD3), D1.52 (VDD4), D1.62 (VDD5), D1.72 (VDD6), D1.84 (VDD7), D1.95 (VDD8), D1.108 (VDD9), D1.121 (VDD10), D1.131 (VDD11), D1.143 (PDR_ON), D1.144 (VDD12), L2.2, L3.2, X1.B3 (3); also elsewhere on the board
+12V: R85.1; also elsewhere on the board
BOOT0: D1.138 (BOOT0), R19.2
GND: C8.2, C9.2, C10.2, C11.2, C12.2, C13.2, C14.2, C15.2, C16.2, C17.2, C18.2, C19.2, C20.2, C21.2, C22.2, C23.2, C24.2, C47.2, C54.2, C55.2, C58.2, D1.16 (VSS1), D1.31 (VSSA), D1.38 (VSS2), D1.51 (VSS3), D1.61 (VSS4), D1.83 (VSS5), D1.94 (VSS6), D1.107 (VSS7), D1.120 (VSS8), D1.130 (VSS9), N3.2 (GND), N3.4 (GND), N3.5 (GND), N3.6 (GND), R19.1, R20.1, R36.1, X1.B2 (2), X1.B4 (4), X1.B5 (5); also elsewhere on the board
INPUT_6: D1.8 (PC14/OSC32IN); also elsewhere on the board
INPUT_7: D1.9 (PC15/OSC32OUT); also elsewhere on the board
MEAS12V: C47.1, D1.34 (PA0/WKUP), R36.2, R85.2
unnamed: D1.109 (PA14/TCK/SWCLK), R4.2
unnamed: D1.105 (PA13/TMS/SWDIO), R3.2
unnamed: C12.1, R17.1
unnamed: D1.48 (PB2/BOOT1), R20.2
OSCIN: C23.1, D1.23 (PH0/OSCIN), G1.1 (X1)
OSCOUT: C24.1, D1.24 (PH1/OSCOUT), G1.3 (X2)
RESETL: D1.25 (RSTL), X1.A1 (1); also elsewhere on the board
SPI1CLK: D1.133 (PB3/TDO); also elsewhere on the board
SPI1MISO: D1.134 (PB4/TRSTL); also elsewhere on the board
SWCLK: R4.1, X1.A3 (3)
SWDIO: R3.1, X1.A2 (2)
USART3RX: X1.A4 (4); also elsewhere on the board
USART3TX: X1.A5 (5); also elsewhere on the board
VCAP1: C9.1, D1.71 (VCAP1)
VCAP2: C8.1, D1.106 (VCAP2)
VDDA: C10.1, C11.1, D1.33 (VDDA), L2.1
VDDAREF: C54.1, C55.1, L3.1, N3.1 (VDD), N3.3 (SHDNL)
VREF25: D1.32 (VREF+), N3.7 (OUT), N3.8 (FEEDBACK), R17.2

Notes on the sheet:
2.5V REFERENCE
SW DEBUG
MAX 20V ~4.97mV/LSB ADC123_in0

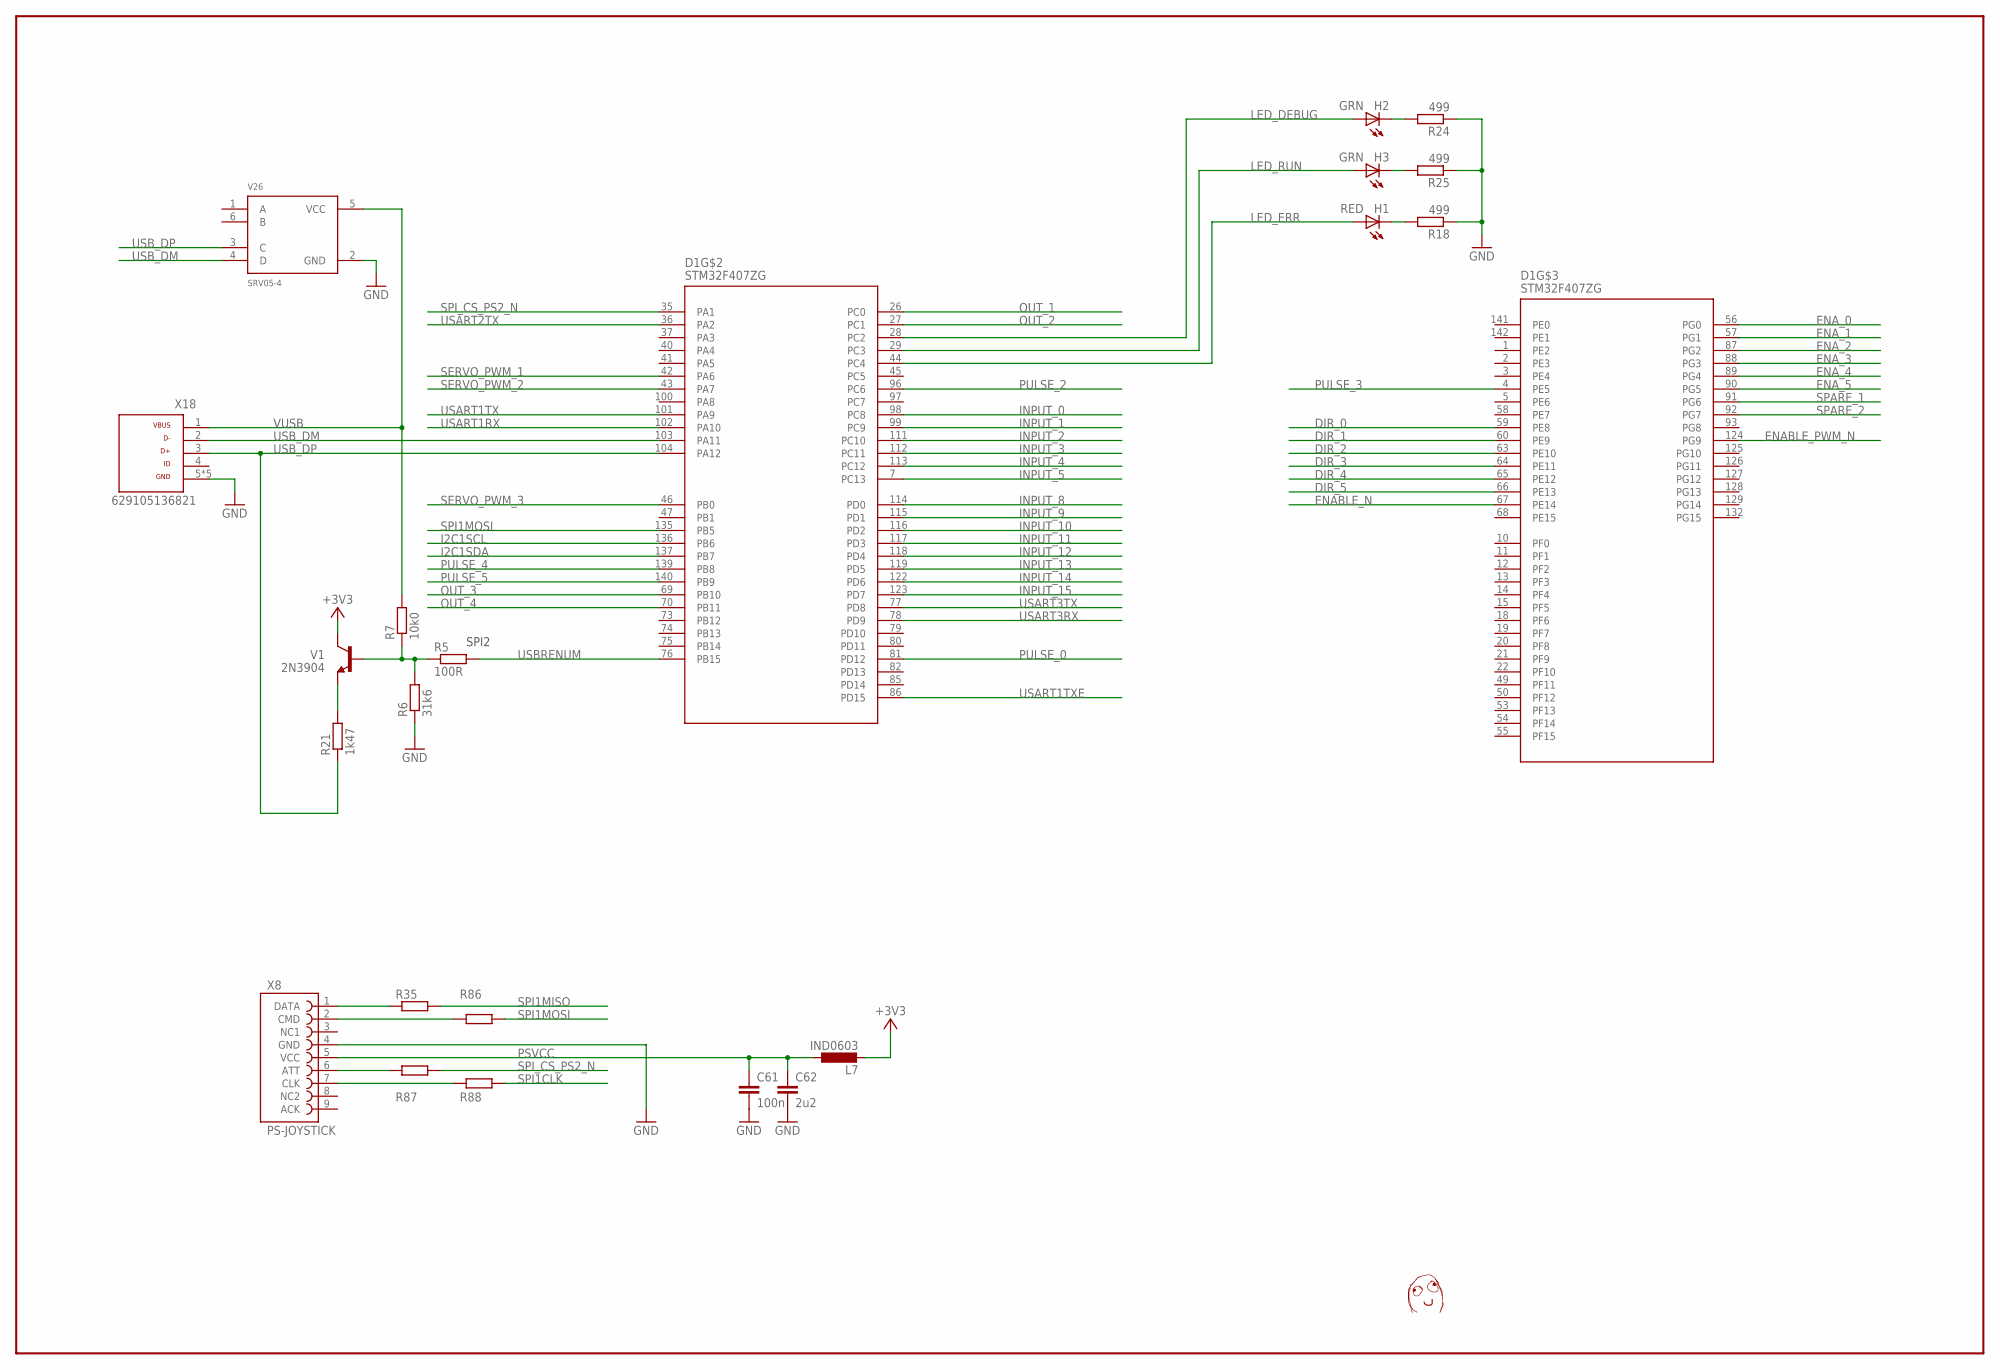
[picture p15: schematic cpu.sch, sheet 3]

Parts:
C61: 100n; C0603
C62: 2u2; C0603
D1: STM32F407ZG; LQFP-144
H1: RED; CHIP-LED0603
H2, H3: GRN; CHIP-LED0603
L7: IND0603; R0603
R5: 100R; PASSIIVIT_R0603
R6: 31k6; PASSIIVIT_R0603
R7: 10k0; PASSIIVIT_R0603
R18, R24, R25: 499; R0603
R21: 1k47; PASSIIVIT_R0603
R35, R86, R87, R88: RES0603; OMAT_IC_2_R0603
U$1: DAFUG
V1: 2N3904; OMAT_IC_2_SOT23
V26: SRV05-4; OMAT_IC_2_SOT23-6
X8: PS-JOYSTICK
X18: 629105136821

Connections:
+3V3: L7.2, V1.3 (C); also elsewhere on the board
DIR_0: D1.59 (PE8); also elsewhere on the board
DIR_1: D1.60 (PE9); also elsewhere on the board
DIR_2: D1.63 (PE10); also elsewhere on the board
DIR_3: D1.64 (PE11); also elsewhere on the board
DIR_4: D1.65 (PE12); also elsewhere on the board
DIR_5: D1.66 (PE13); also elsewhere on the board
ENABLE_N: D1.67 (PE14); also elsewhere on the board
ENABLE_PWM_N: D1.124 (PG9); also elsewhere on the board
ENA_0: D1.56 (PG0); also elsewhere on the board
ENA_1: D1.57 (PG1); also elsewhere on the board
ENA_2: D1.87 (PG2); also elsewhere on the board
ENA_3: D1.88 (PG3); also elsewhere on the board
ENA_4: D1.89 (PG4); also elsewhere on the board
ENA_5: D1.90 (PG5); also elsewhere on the board
GND: C61.2, C62.2, R6.1, R18.1, R24.1, R25.1, V26.2 (GND), X8.4 (GND), X18.5, X18.Z1 (5), X18.Z2 (5), X18.Z3 (5), X18.Z4 (5); also elsewhere on the board
I2C1SCL: D1.136 (PB6); also elsewhere on the board
I2C1SDA: D1.137 (PB7); also elsewhere on the board
INPUT_0: D1.98 (PC8); also elsewhere on the board
INPUT_1: D1.99 (PC9); also elsewhere on the board
INPUT_2: D1.111 (PC10); also elsewhere on the board
INPUT_3: D1.112 (PC11); also elsewhere on the board
INPUT_4: D1.113 (PC12); also elsewhere on the board
INPUT_5: D1.7 (PC13); also elsewhere on the board
INPUT_8: D1.114 (PD0); also elsewhere on the board
INPUT_9: D1.115 (PD1); also elsewhere on the board
INPUT_10: D1.116 (PD2); also elsewhere on the board
INPUT_11: D1.117 (PD3); also elsewhere on the board
INPUT_12: D1.118 (PD4); also elsewhere on the board
INPUT_13: D1.119 (PD5); also elsewhere on the board
INPUT_14: D1.122 (PD6); also elsewhere on the board
INPUT_15: D1.123 (PD7); also elsewhere on the board
LED_DEBUG: D1.28 (PC2), H2.A
LED_ERR: D1.44 (PC4), H1.A
LED_RUN: D1.29 (PC3), H3.A
unnamed: R35.1, X8.1 (DATA)
unnamed: R5.1, R6.2, R7.1, V1.1 (B)
unnamed: R21.2, V1.2 (E)
unnamed: R86.1, X8.2 (CMD)
unnamed: H2.C, R24.2
unnamed: H1.C, R18.2
unnamed: H3.C, R25.2
unnamed: R87.1, X8.6 (ATT)
unnamed: R88.1, X8.7 (CLK)
OUT_1: D1.26 (PC0); also elsewhere on the board
OUT_2: D1.27 (PC1); also elsewhere on the board
OUT_3: D1.69 (PB10); also elsewhere on the board
OUT_4: D1.70 (PB11); also elsewhere on the board
PSVCC: C61.1, C62.1, L7.1, X8.5 (VCC)
PULSE_0: D1.81 (PD12); also elsewhere on the board
PULSE_2: D1.96 (PC6); also elsewhere on the board
PULSE_3: D1.4 (PE5); also elsewhere on the board
PULSE_4: D1.139 (PB8); also elsewhere on the board
PULSE_5: D1.140 (PB9); also elsewhere on the board
SERVO_PWM_1: D1.42 (PA6); also elsewhere on the board
SERVO_PWM_2: D1.43 (PA7); also elsewhere on the board
SERVO_PWM_3: D1.46 (PB0); also elsewhere on the board
SPARE_1: D1.91 (PG6); also elsewhere on the board
SPARE_2: D1.92 (PG7); also elsewhere on the board
SPI1CLK: R88.2; also elsewhere on the board
SPI1MISO: R35.2; also elsewhere on the board
SPI1MOSI: D1.135 (PB5), R86.2
SPI_CS_PS2_N: D1.35 (PA1), R87.2
USART1RX: D1.102 (PA10); also elsewhere on the board
USART1TX: D1.101 (PA9); also elsewhere on the board
USART1TXE: D1.86 (PD15); also elsewhere on the board
USART2TX: D1.36 (PA2); also elsewhere on the board
USART3RX: D1.78 (PD9); also elsewhere on the board
USART3TX: D1.77 (PD8); also elsewhere on the board
USBRENUM: D1.76 (PB15), R5.2
USB_DM: D1.103 (PA11), V26.4 (D), X18.2
USB_DP: D1.104 (PA12), R21.1, V26.3 (C), X18.3
VUSB: R7.2, V26.5 (VCC), X18.1

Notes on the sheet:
SPI2

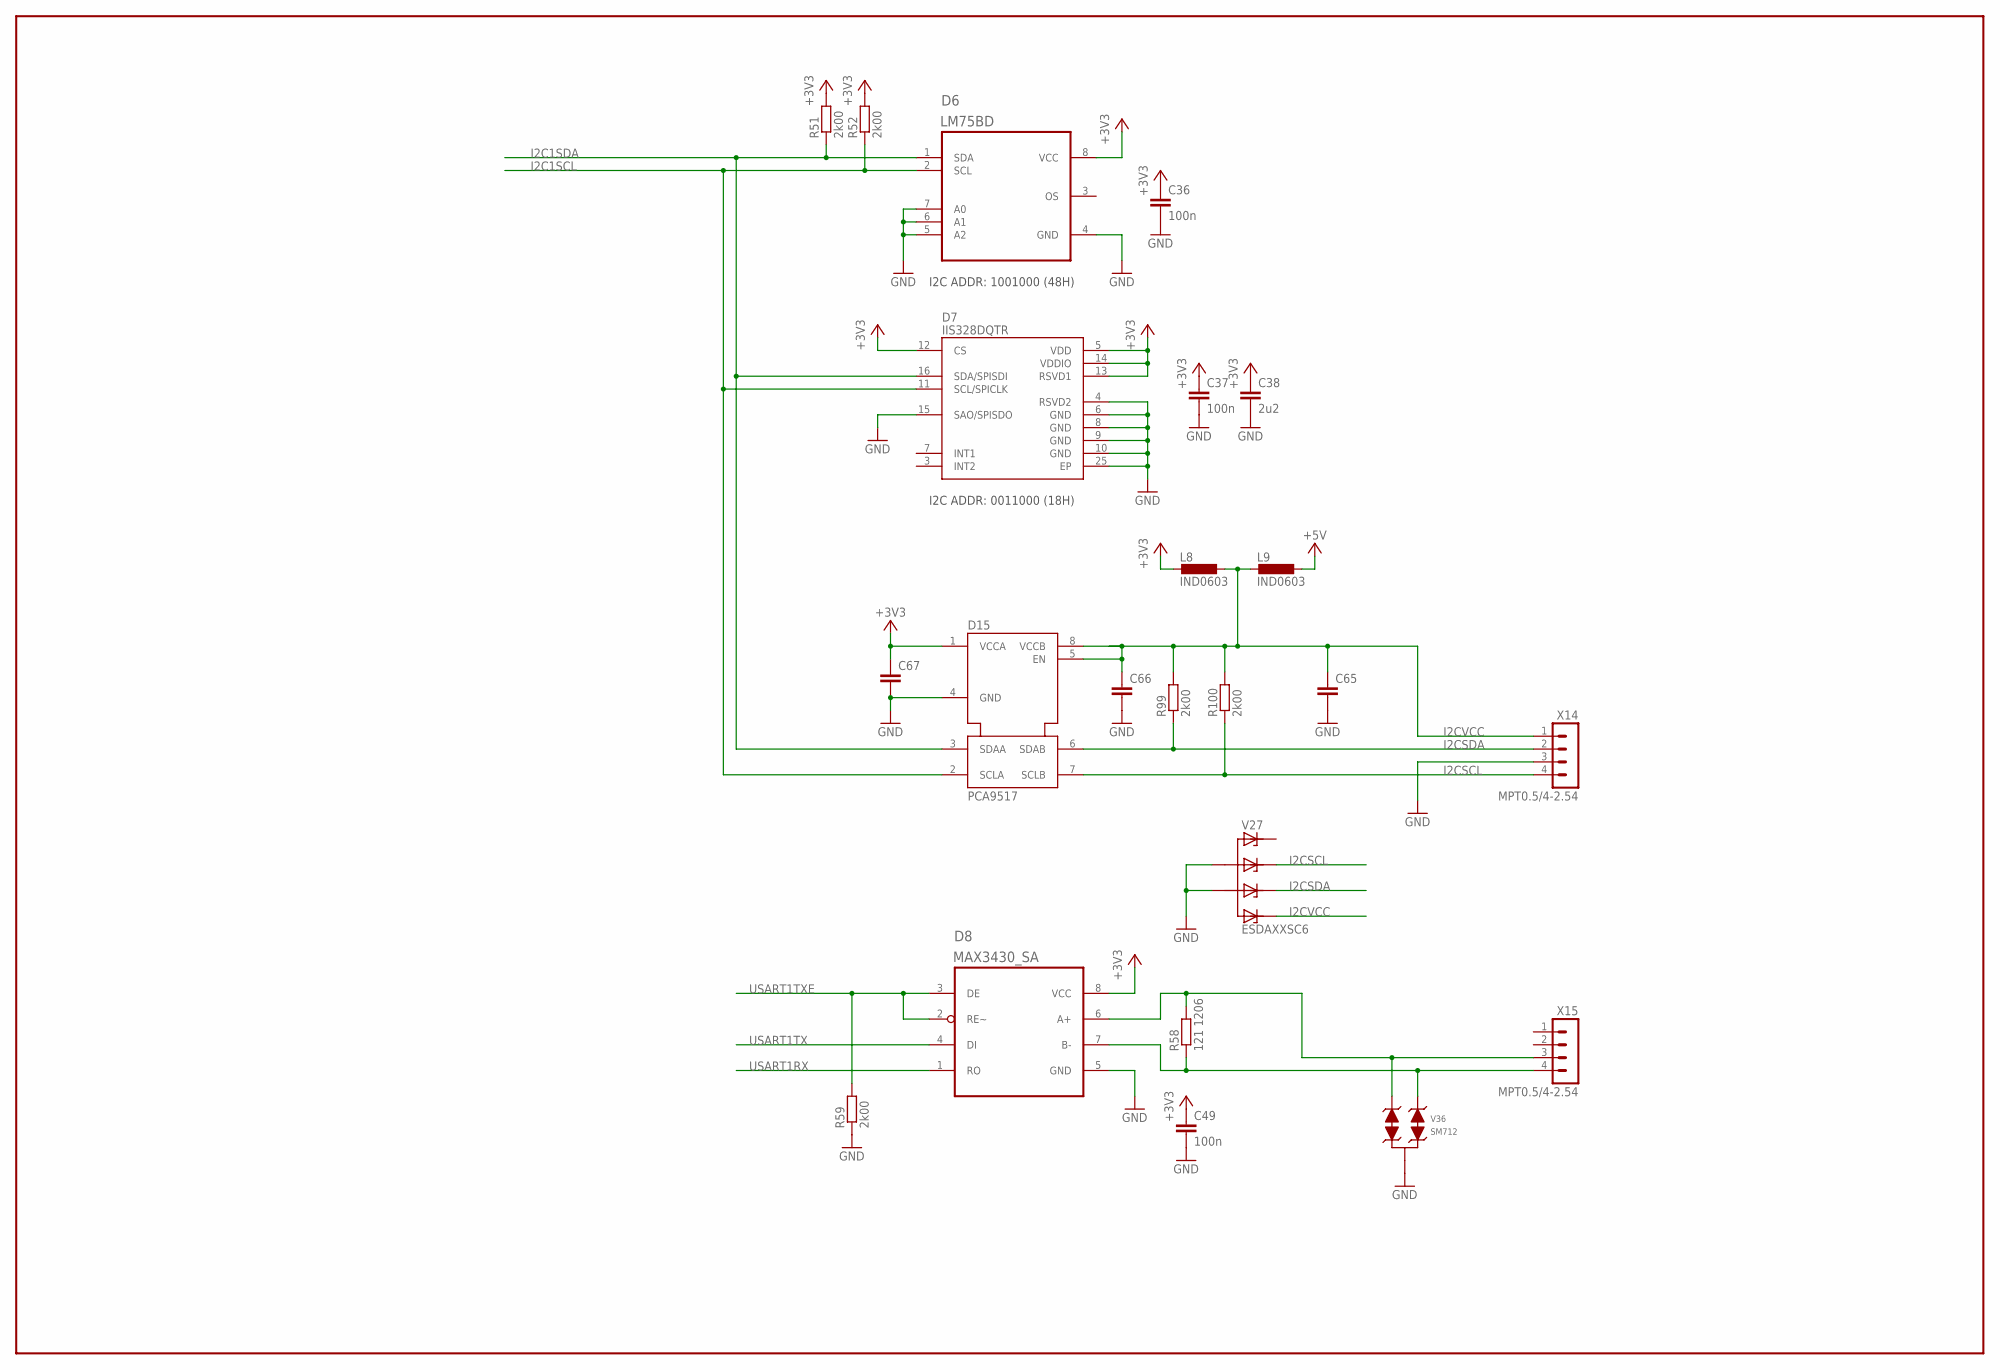
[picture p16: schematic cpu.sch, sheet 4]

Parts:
C36, C37, C49: 100n; C0603
C38: 2u2; C0603
C65, C66, C67: CAP0805; OMAT_IC_2_C0805
D6: LM75BD; SOIC8-N_MC
D7: IIS328DQTR; QFN50P400X400X100-25N
D8: MAX3430_SA; SOIC8-N_MC
D15: PCA9517; OMAT_IC_2_SOIC8-N_MC
L8, L9: IND0603; OMAT_IC_2_R0603
R51, R52, R59, R99, R100: 2k00; R0603
R58: 121 1206; R1206
V27: ESDAXXSC6; OMAT_IC_2_SOT23-6
V36: SM712; SOT23
X14, X15: MPT0.5/4-2.54

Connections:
+3V3: C36.1, C37.1, C38.1, C49.1, C67.1, D6.8 (VCC), D7.5 (VDD), D7.12 (CS), D7.13 (RSVD1), D7.14 (VDDIO), D8.8 (VCC), D15.1 (VCCA), L8.2, R51.2, R52.2; also elsewhere on the board
+5V: L9.1; also elsewhere on the board
ACCRTXHI: D8.6 (A+), R58.2, V36.2, X15.3
ACCRTXLO: D8.7 (B-), R58.1, V36.1, X15.4
GND: C36.2, C37.2, C38.2, C49.2, C65.2, C66.2, C67.2, D6.4 (GND), D6.5 (A2), D6.6 (A1), D6.7 (A0), D7.4 (RSVD2), D7.6 (GND), D7.8 (GND), D7.9 (GND), D7.10 (GND), D7.15 (SAO/SPISDO), D7.25 (EP), D8.5 (GND), D15.4 (GND), R59.1, V27.2 (A), V27.5 (A1), V36.3, X14.3; also elsewhere on the board
I2C1SCL: D6.2 (SCL), D7.11 (SCL/SPICLK), D15.2 (SCLA), R52.1; also elsewhere on the board
I2C1SDA: D6.1 (SDA), D7.16 (SDA/SPISDI), D15.3 (SDAA), R51.1; also elsewhere on the board
I2CSCL: D15.7 (SCLB), R100.1, V27.3 (C1), X14.4
I2CSDA: D15.6 (SDAB), R99.1, V27.4 (C2), X14.2
I2CVCC: C65.1, C66.1, D15.5 (EN), D15.8 (VCCB), L8.1, L9.2, R99.2, R100.2, V27.6 (C3), X14.1
USART1RX: D8.1 (RO); also elsewhere on the board
USART1TX: D8.4 (DI); also elsewhere on the board
USART1TXE: D8.2 (RE~), D8.3 (DE), R59.2; also elsewhere on the board

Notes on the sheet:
I2C ADDR: 1001000 (48H)
I2C ADDR: 0011000 (18H)

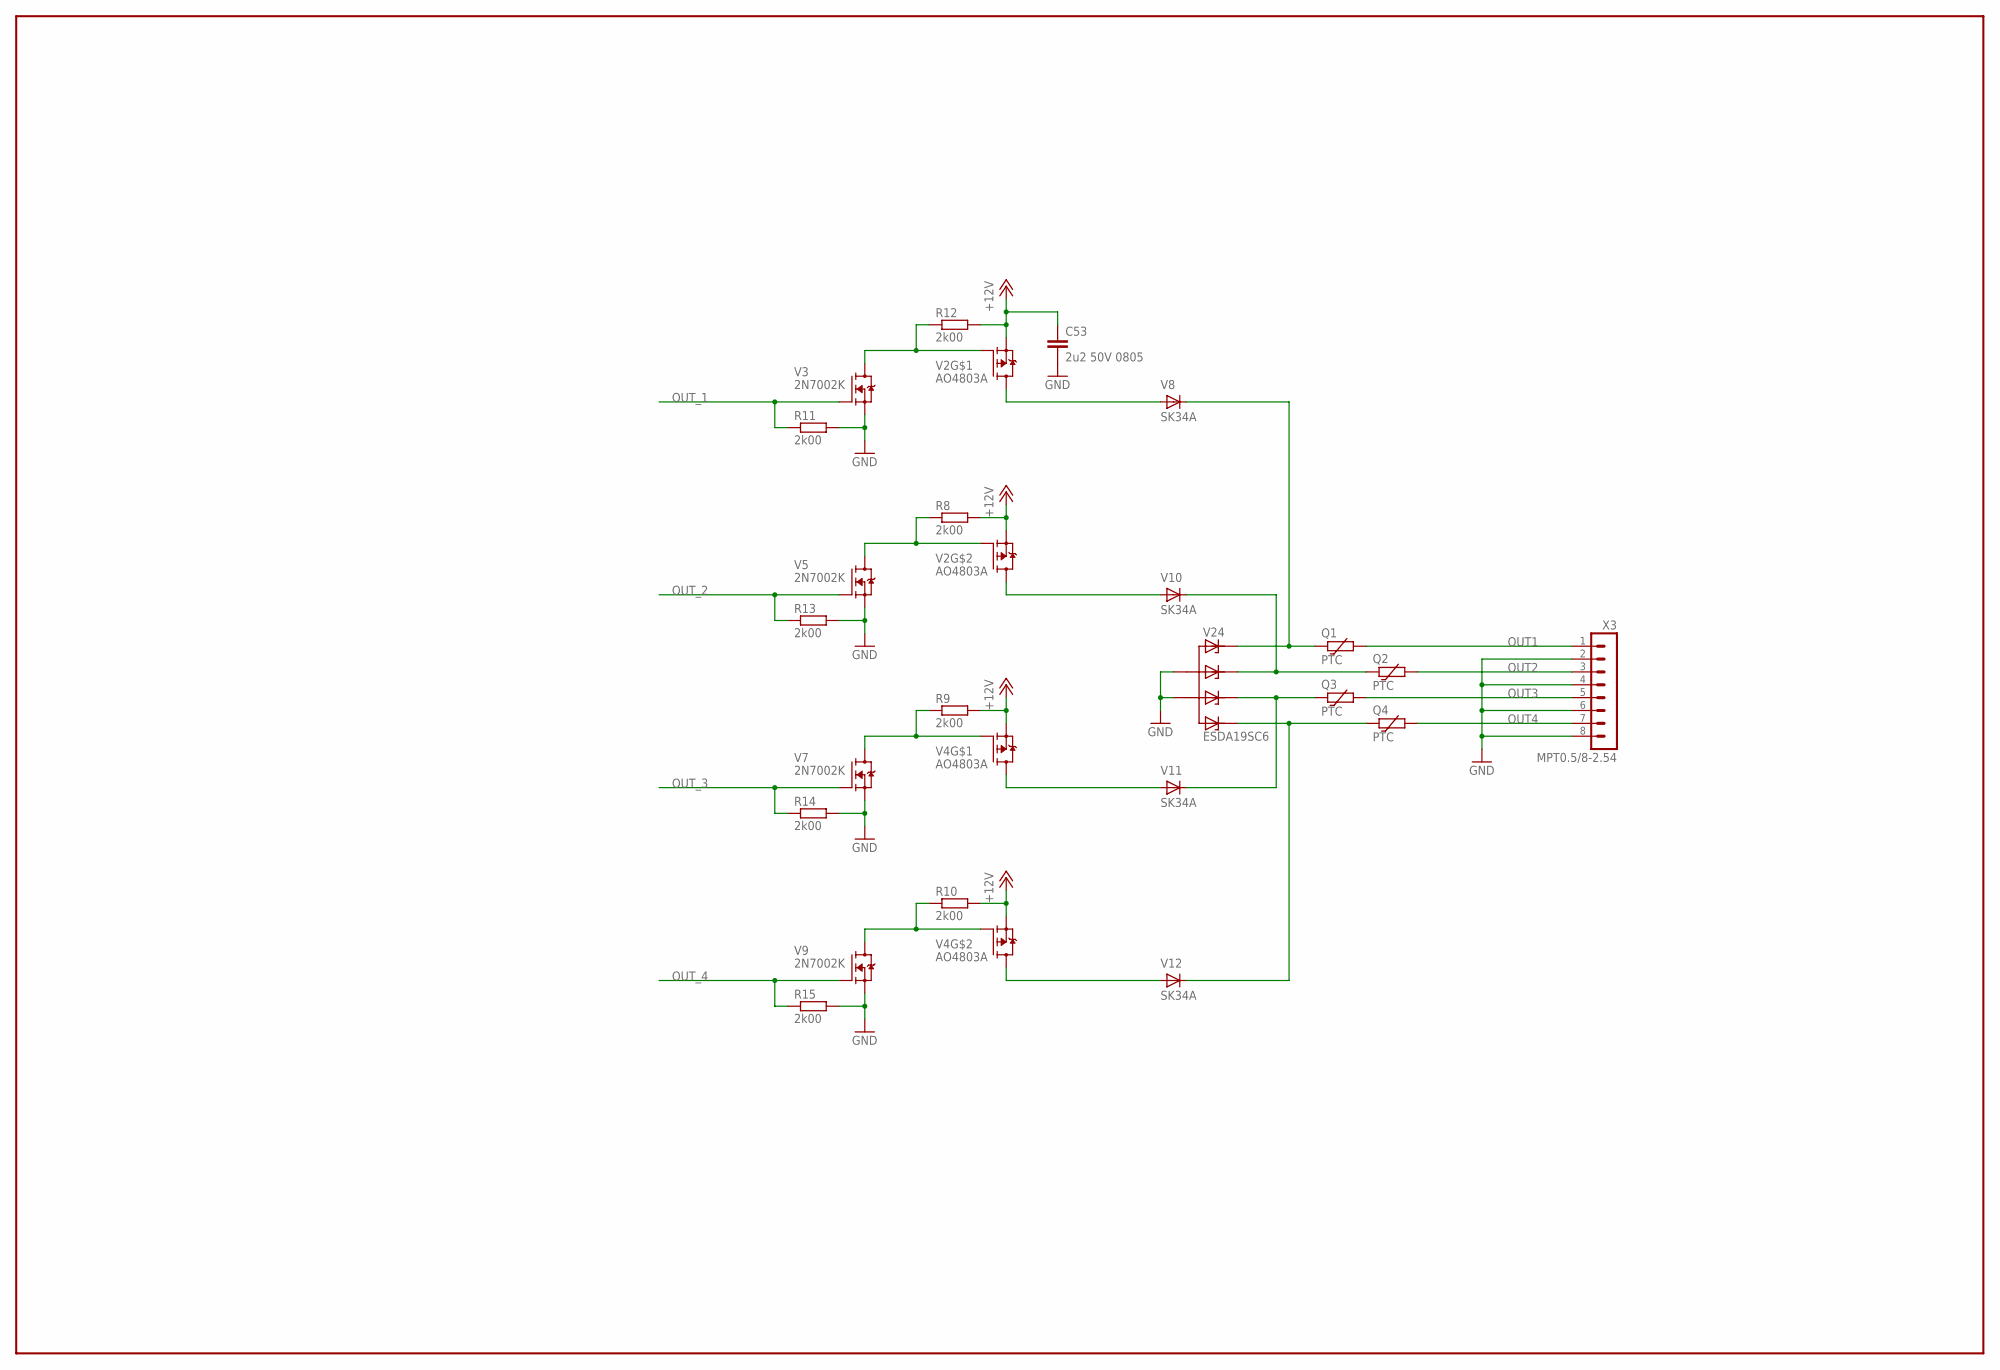
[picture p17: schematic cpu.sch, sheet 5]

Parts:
C53: 2u2 50V 0805; C0805
Q1, Q2, Q3, Q4: PTC; OMAT_IC_2_R1812
R8, R9, R10, R11, R12, R13, R14, R15: 2k00; R0603
V2, V4: AO4803A; SOIC8-N_MC
V3, V5, V7, V9: 2N7002K; SOT23
V8, V10, V11, V12: SK34A; DO214AC
V24: ESDA19SC6; SOT23-6
X3: MPT0.5/8-2.54

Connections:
+12V: C53.1, R8.2, R9.2, R10.2, R12.2, V2.1 (S), V2.3 (S), V4.1 (S), V4.3 (S); also elsewhere on the board
GND: C53.2, R11.2, R13.2, R14.2, R15.2, V3.2 (S), V5.2 (S), V7.2 (S), V9.2 (S), V24.2 (A), V24.5 (A1), X3.2, X3.4, X3.6, X3.8; also elsewhere on the board
unnamed: R8.1, V2.2 (G), V5.3 (D)
unnamed: R12.1, V2.4 (G), V3.3 (D)
unnamed: R9.1, V4.4 (G), V7.3 (D)
unnamed: R10.1, V4.2 (G), V9.3 (D)
NERT: V2.5 (D), V2.6 (D), V8.A
NERT1: V2.7 (D), V2.8 (D), V10.A
NERT2: V4.5 (D), V4.6 (D), V11.A
NERT3: V4.7 (D), V4.8 (D), V12.A
OUT1: Q1.2, X3.1
OUT1X: Q1.1, V8.C, V24.1 (C)
OUT2: Q2.2, X3.3
OUT2X: Q2.1, V10.C, V24.3 (C1)
OUT3: Q3.2, X3.5
OUT3X: Q3.1, V11.C, V24.4 (C2)
OUT4: Q4.2, X3.7
OUT4X: Q4.1, V12.C, V24.6 (C3)
OUT_1: R11.1, V3.1 (G); also elsewhere on the board
OUT_2: R13.1, V5.1 (G); also elsewhere on the board
OUT_3: R14.1, V7.1 (G); also elsewhere on the board
OUT_4: R15.1, V9.1 (G); also elsewhere on the board

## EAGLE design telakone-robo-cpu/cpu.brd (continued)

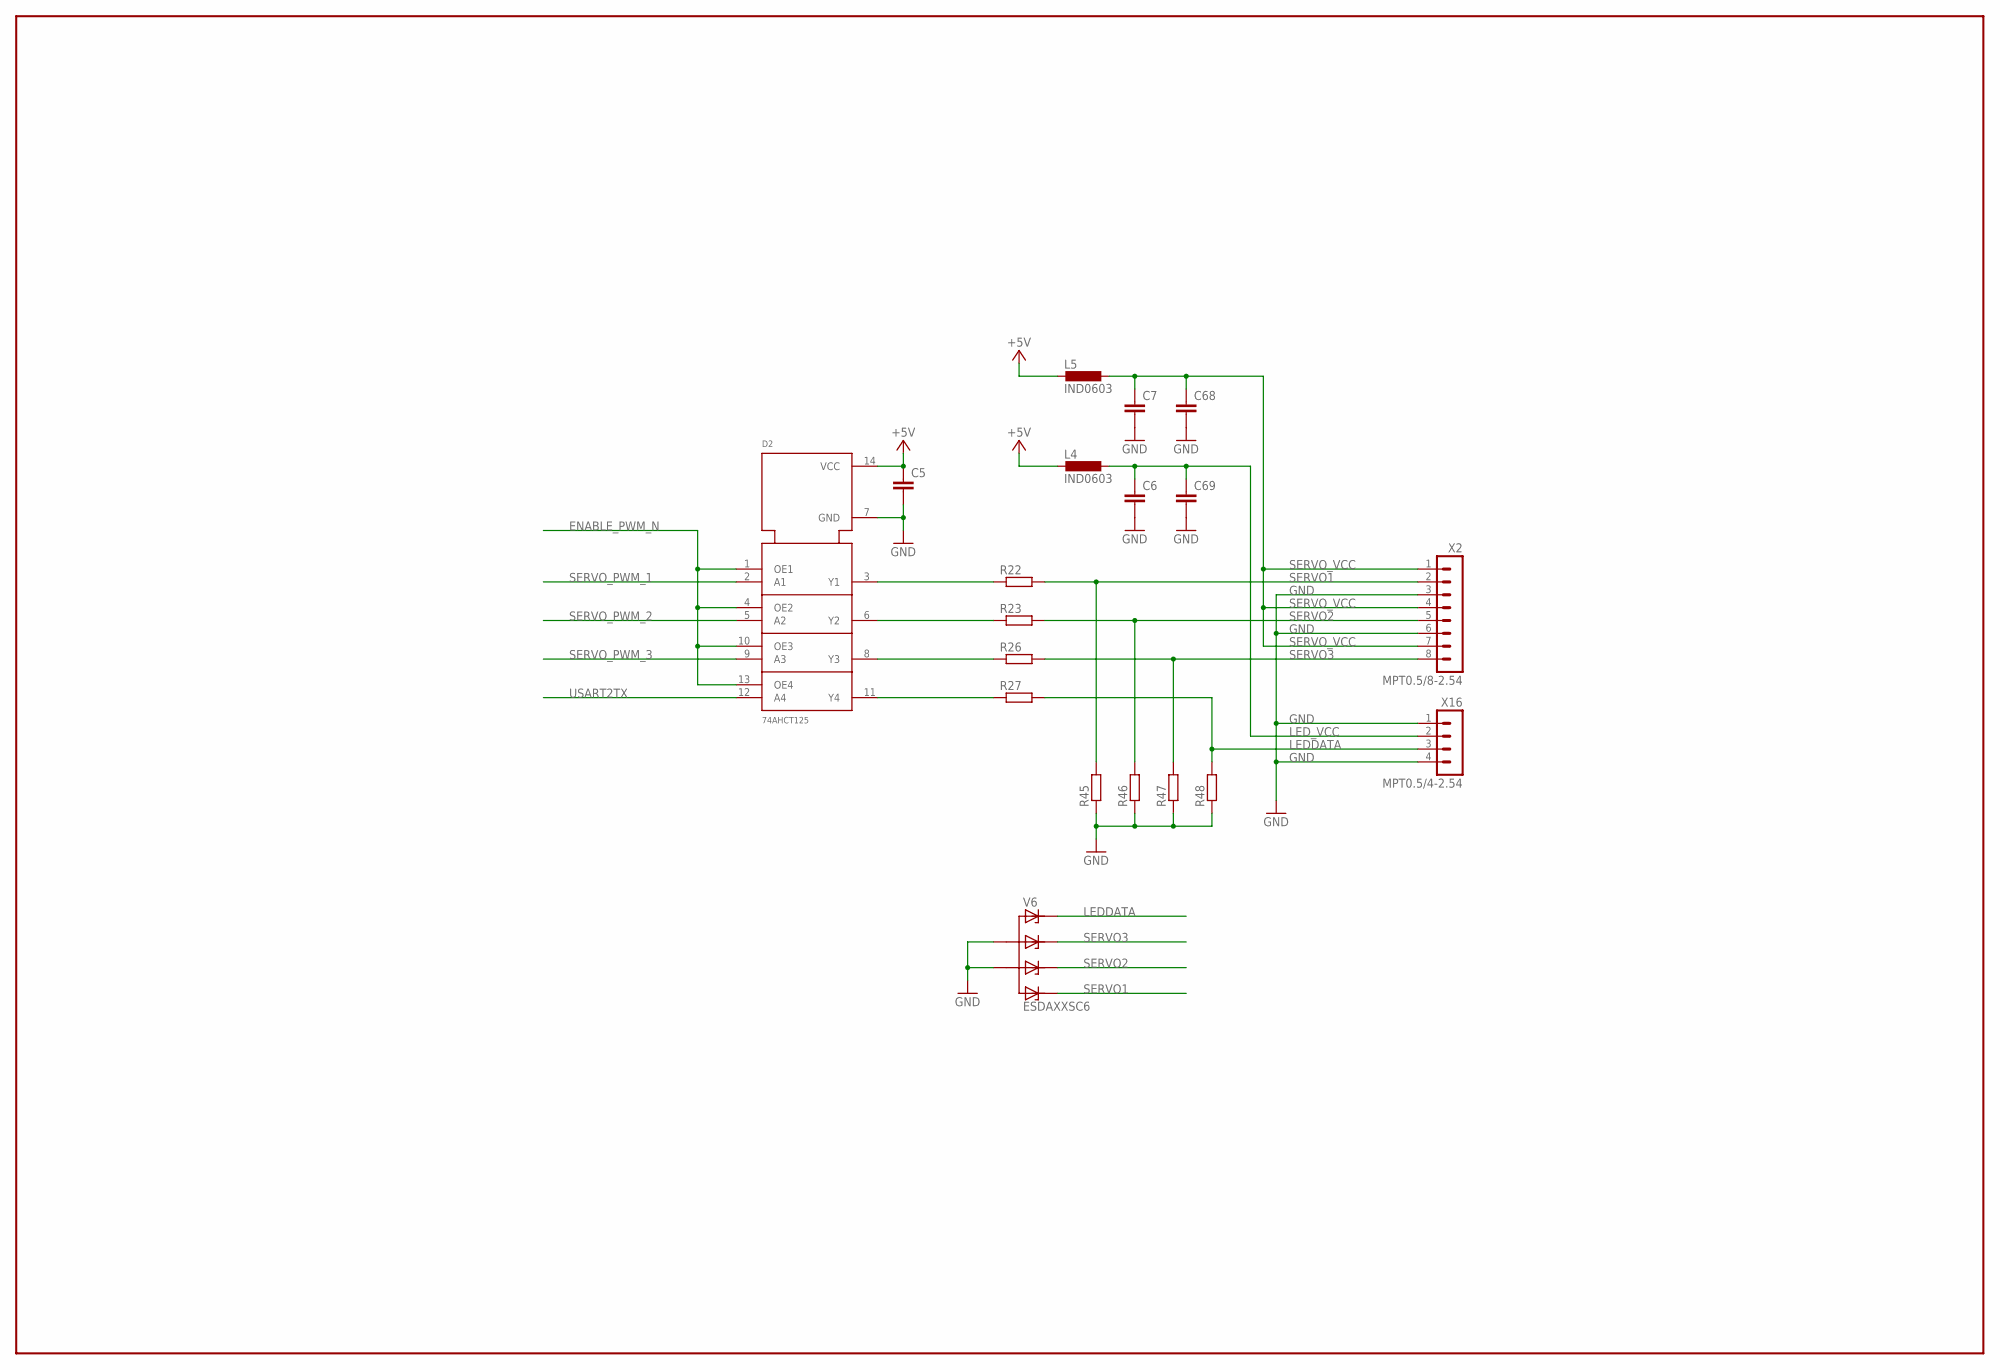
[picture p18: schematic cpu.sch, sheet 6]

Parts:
C5: CAP0603; OMAT_IC_2_C0603
C6, C7, C68, C69: CAP0805; OMAT_IC_2_C0805
D2: 74AHCT125; SO14
L4, L5: IND0603; OMAT_IC_2_R0603
R22, R23, R26, R27, R45, R46, R47, R48: RES0603; OMAT_IC_2_R0603
V6: ESDAXXSC6; OMAT_IC_2_SOT23-6
X2: MPT0.5/8-2.54; OMAT_IC_2_MPT0.5/8-2.54
X16: MPT0.5/4-2.54

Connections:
+5V: C5.1, D2.14 (VCC), L4.2, L5.2; also elsewhere on the board
ENABLE_PWM_N: D2.1 (OE1), D2.4 (OE2), D2.10 (OE3), D2.13 (OE4); also elsewhere on the board
GND: C5.2, C6.2, C7.2, C68.2, C69.2, D2.7 (GND), R45.1, R46.1, R47.1, R48.1, V6.2 (A), V6.5 (A1), X2.3, X2.6, X16.1, X16.4; also elsewhere on the board
LEDDATA: R27.2, R48.2, V6.1 (C), X16.3
LED_VCC: C6.1, C69.1, L4.1, X16.2
unnamed: D2.3 (Y1), R22.1
unnamed: D2.6 (Y2), R23.1
unnamed: D2.8 (Y3), R26.1
unnamed: D2.11 (Y4), R27.1
SERVO1: R22.2, R45.2, V6.6 (C3), X2.2
SERVO2: R23.2, R46.2, V6.4 (C2), X2.5
SERVO3: R26.2, R47.2, V6.3 (C1), X2.8
SERVO_PWM_1: D2.2 (A1); also elsewhere on the board
SERVO_PWM_2: D2.5 (A2); also elsewhere on the board
SERVO_PWM_3: D2.9 (A3); also elsewhere on the board
SERVO_VCC: C7.1, C68.1, L5.1, X2.1, X2.4, X2.7
USART2TX: D2.12 (A4); also elsewhere on the board

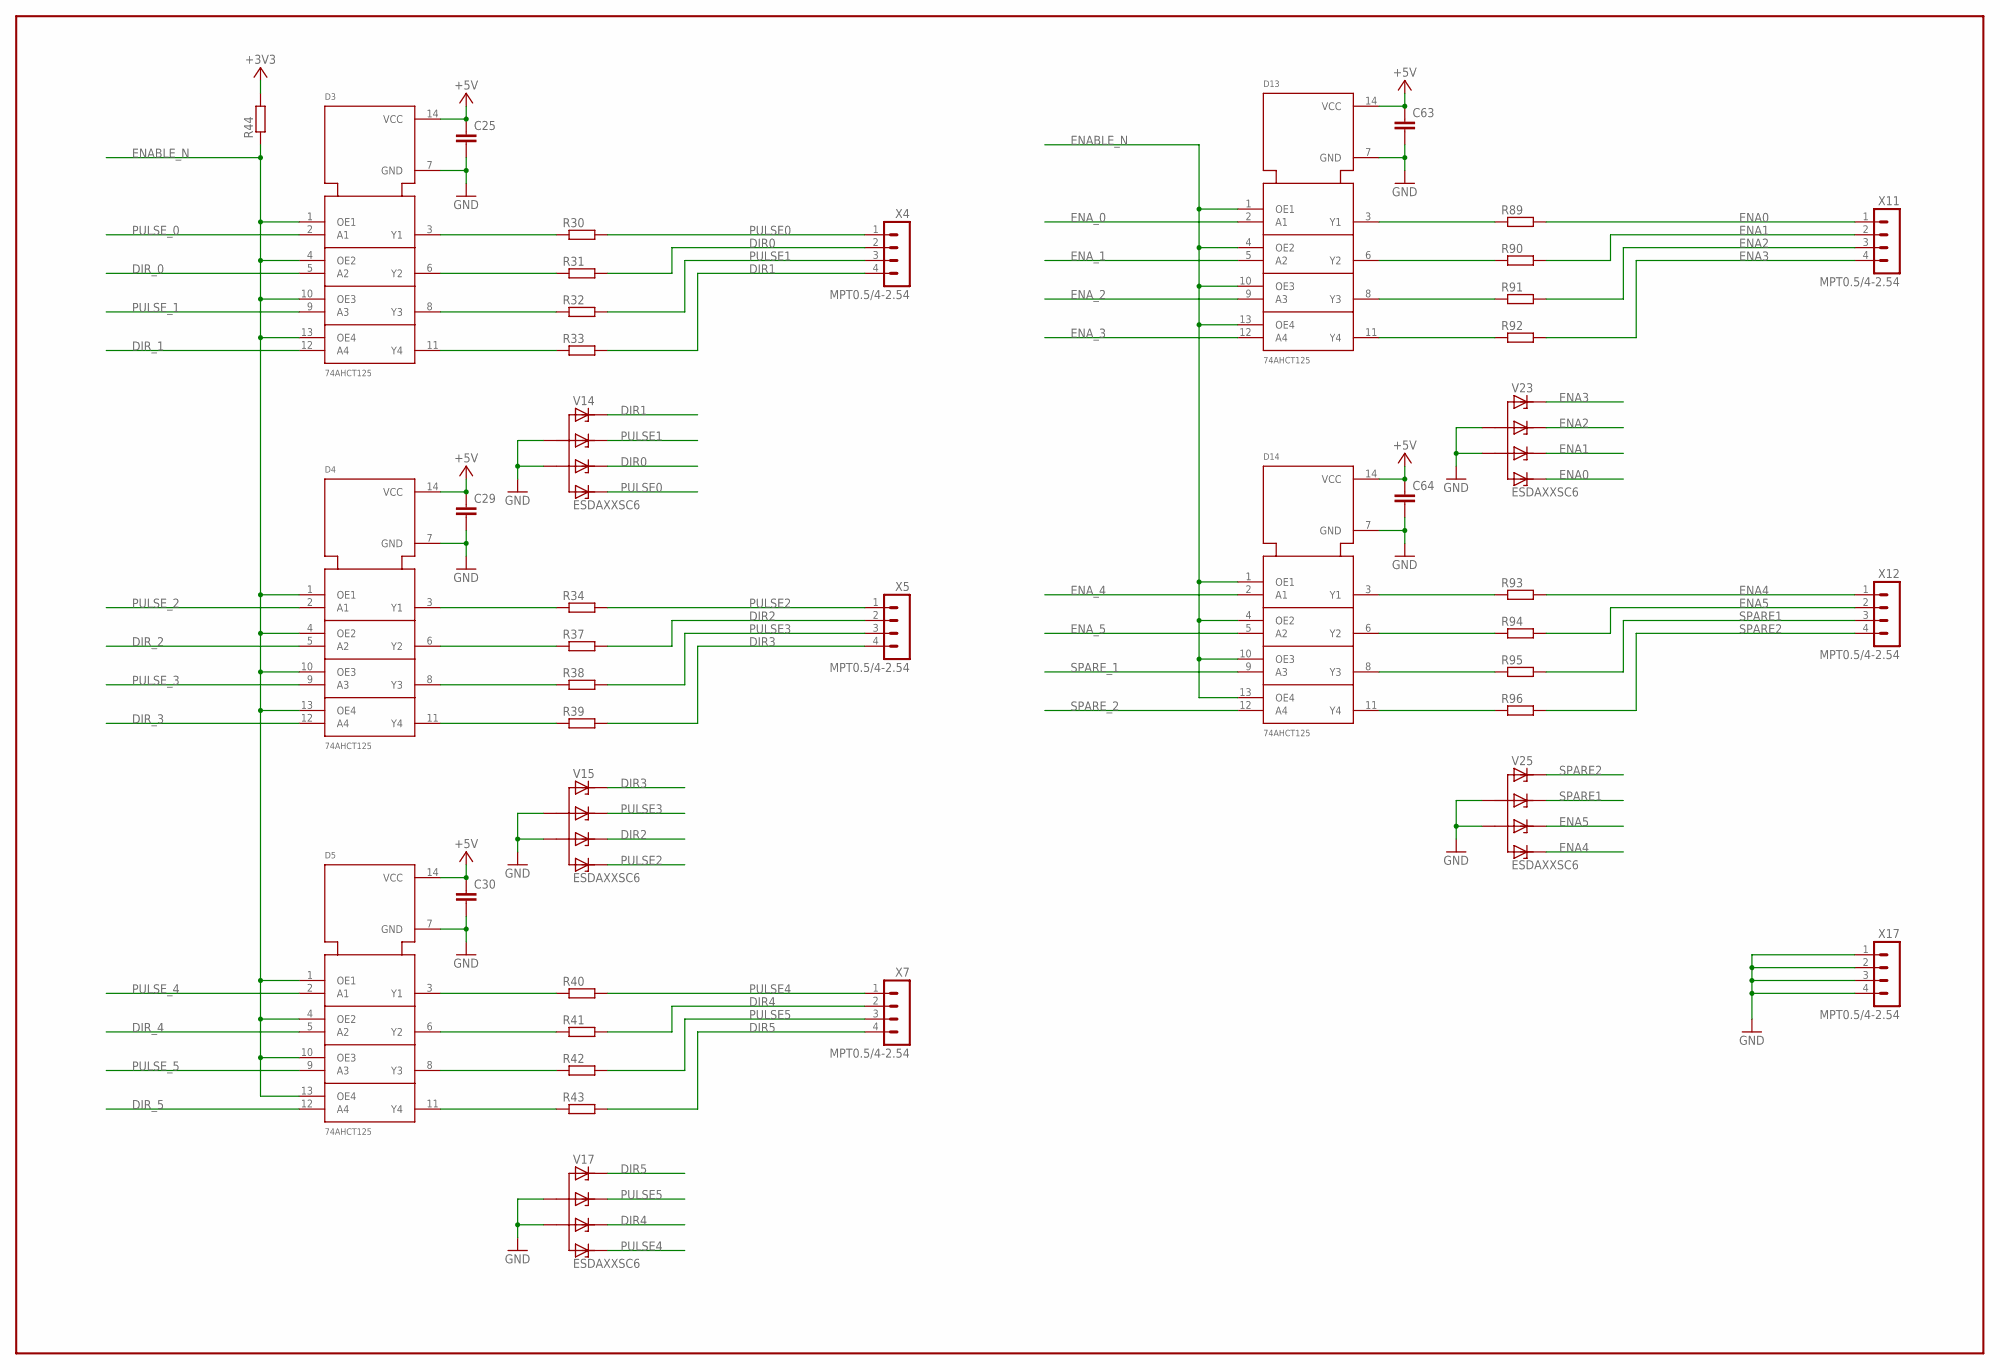
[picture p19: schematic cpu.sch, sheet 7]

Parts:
C25, C29, C30, C63, C64: CAP0603; OMAT_IC_2_C0603
D3, D4, D5, D13, D14: 74AHCT125; SO14
R30, R31, R32, R33, R34, R37, R38, R39, R40, R41, R42, R43, R44, R89, R90, R91, R92, R93, R94, R95, R96: RES0603; OMAT_IC_2_R0603
V14, V15, V17, V23, V25: ESDAXXSC6; OMAT_IC_2_SOT23-6
X4, X5, X7, X11, X12, X17: MPT0.5/4-2.54

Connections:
+3V3: R44.2; also elsewhere on the board
+5V: C25.1, C29.1, C30.1, C63.1, C64.1, D3.14 (VCC), D4.14 (VCC), D5.14 (VCC), D13.14 (VCC), D14.14 (VCC); also elsewhere on the board
DIR0: R31.2, V14.4 (C2), X4.2
DIR1: R33.2, V14.1 (C), X4.4
DIR2: R37.2, V15.4 (C2), X5.2
DIR3: R39.2, V15.1 (C), X5.4
DIR4: R41.2, V17.4 (C2), X7.2
DIR5: R43.2, V17.1 (C), X7.4
DIR_0: D3.5 (A2); also elsewhere on the board
DIR_1: D3.12 (A4); also elsewhere on the board
DIR_2: D4.5 (A2); also elsewhere on the board
DIR_3: D4.12 (A4); also elsewhere on the board
DIR_4: D5.5 (A2); also elsewhere on the board
DIR_5: D5.12 (A4); also elsewhere on the board
ENA0: R89.2, V23.6 (C3), X11.1
ENA1: R90.2, V23.4 (C2), X11.2
ENA2: R91.2, V23.3 (C1), X11.3
ENA3: R92.2, V23.1 (C), X11.4
ENA4: R93.2, V25.6 (C3), X12.1
ENA5: R94.2, V25.4 (C2), X12.2
ENABLE_N: D3.1 (OE1), D3.4 (OE2), D3.10 (OE3), D3.13 (OE4), D4.1 (OE1), D4.4 (OE2), D4.10 (OE3), D4.13 (OE4), D5.1 (OE1), D5.4 (OE2), D5.10 (OE3), D5.13 (OE4), D13.1 (OE1), D13.4 (OE2), D13.10 (OE3), D13.13 (OE4), D14.1 (OE1), D14.4 (OE2), D14.10 (OE3), D14.13 (OE4), R44.1; also elsewhere on the board
ENA_0: D13.2 (A1); also elsewhere on the board
ENA_1: D13.5 (A2); also elsewhere on the board
ENA_2: D13.9 (A3); also elsewhere on the board
ENA_3: D13.12 (A4); also elsewhere on the board
ENA_4: D14.2 (A1); also elsewhere on the board
ENA_5: D14.5 (A2); also elsewhere on the board
GND: C25.2, C29.2, C30.2, C63.2, C64.2, D3.7 (GND), D4.7 (GND), D5.7 (GND), D13.7 (GND), D14.7 (GND), V14.2 (A), V14.5 (A1), V15.2 (A), V15.5 (A1), V17.2 (A), V17.5 (A1), V23.2 (A), V23.5 (A1), V25.2 (A), V25.5 (A1), X17.1, X17.2, X17.3, X17.4; also elsewhere on the board
unnamed: D3.3 (Y1), R30.1
unnamed: D3.6 (Y2), R31.1
unnamed: D3.8 (Y3), R32.1
unnamed: D3.11 (Y4), R33.1
unnamed: D4.3 (Y1), R34.1
unnamed: D4.6 (Y2), R37.1
unnamed: D4.8 (Y3), R38.1
unnamed: D4.11 (Y4), R39.1
unnamed: D5.3 (Y1), R40.1
unnamed: D5.6 (Y2), R41.1
unnamed: D5.8 (Y3), R42.1
unnamed: D5.11 (Y4), R43.1
unnamed: D13.3 (Y1), R89.1
unnamed: D13.6 (Y2), R90.1
unnamed: D13.8 (Y3), R91.1
unnamed: D13.11 (Y4), R92.1
unnamed: D14.3 (Y1), R93.1
unnamed: D14.6 (Y2), R94.1
unnamed: D14.8 (Y3), R95.1
unnamed: D14.11 (Y4), R96.1
PULSE0: R30.2, V14.6 (C3), X4.1
PULSE1: R32.2, V14.3 (C1), X4.3
PULSE2: R34.2, V15.6 (C3), X5.1
PULSE3: R38.2, V15.3 (C1), X5.3
PULSE4: R40.2, V17.6 (C3), X7.1
PULSE5: R42.2, V17.3 (C1), X7.3
PULSE_0: D3.2 (A1); also elsewhere on the board
PULSE_1: D3.9 (A3)
PULSE_2: D4.2 (A1); also elsewhere on the board
PULSE_3: D4.9 (A3); also elsewhere on the board
PULSE_4: D5.2 (A1); also elsewhere on the board
PULSE_5: D5.9 (A3); also elsewhere on the board
SPARE1: R95.2, V25.3 (C1), X12.3
SPARE2: R96.2, V25.1 (C), X12.4
SPARE_1: D14.9 (A3); also elsewhere on the board
SPARE_2: D14.12 (A4); also elsewhere on the board

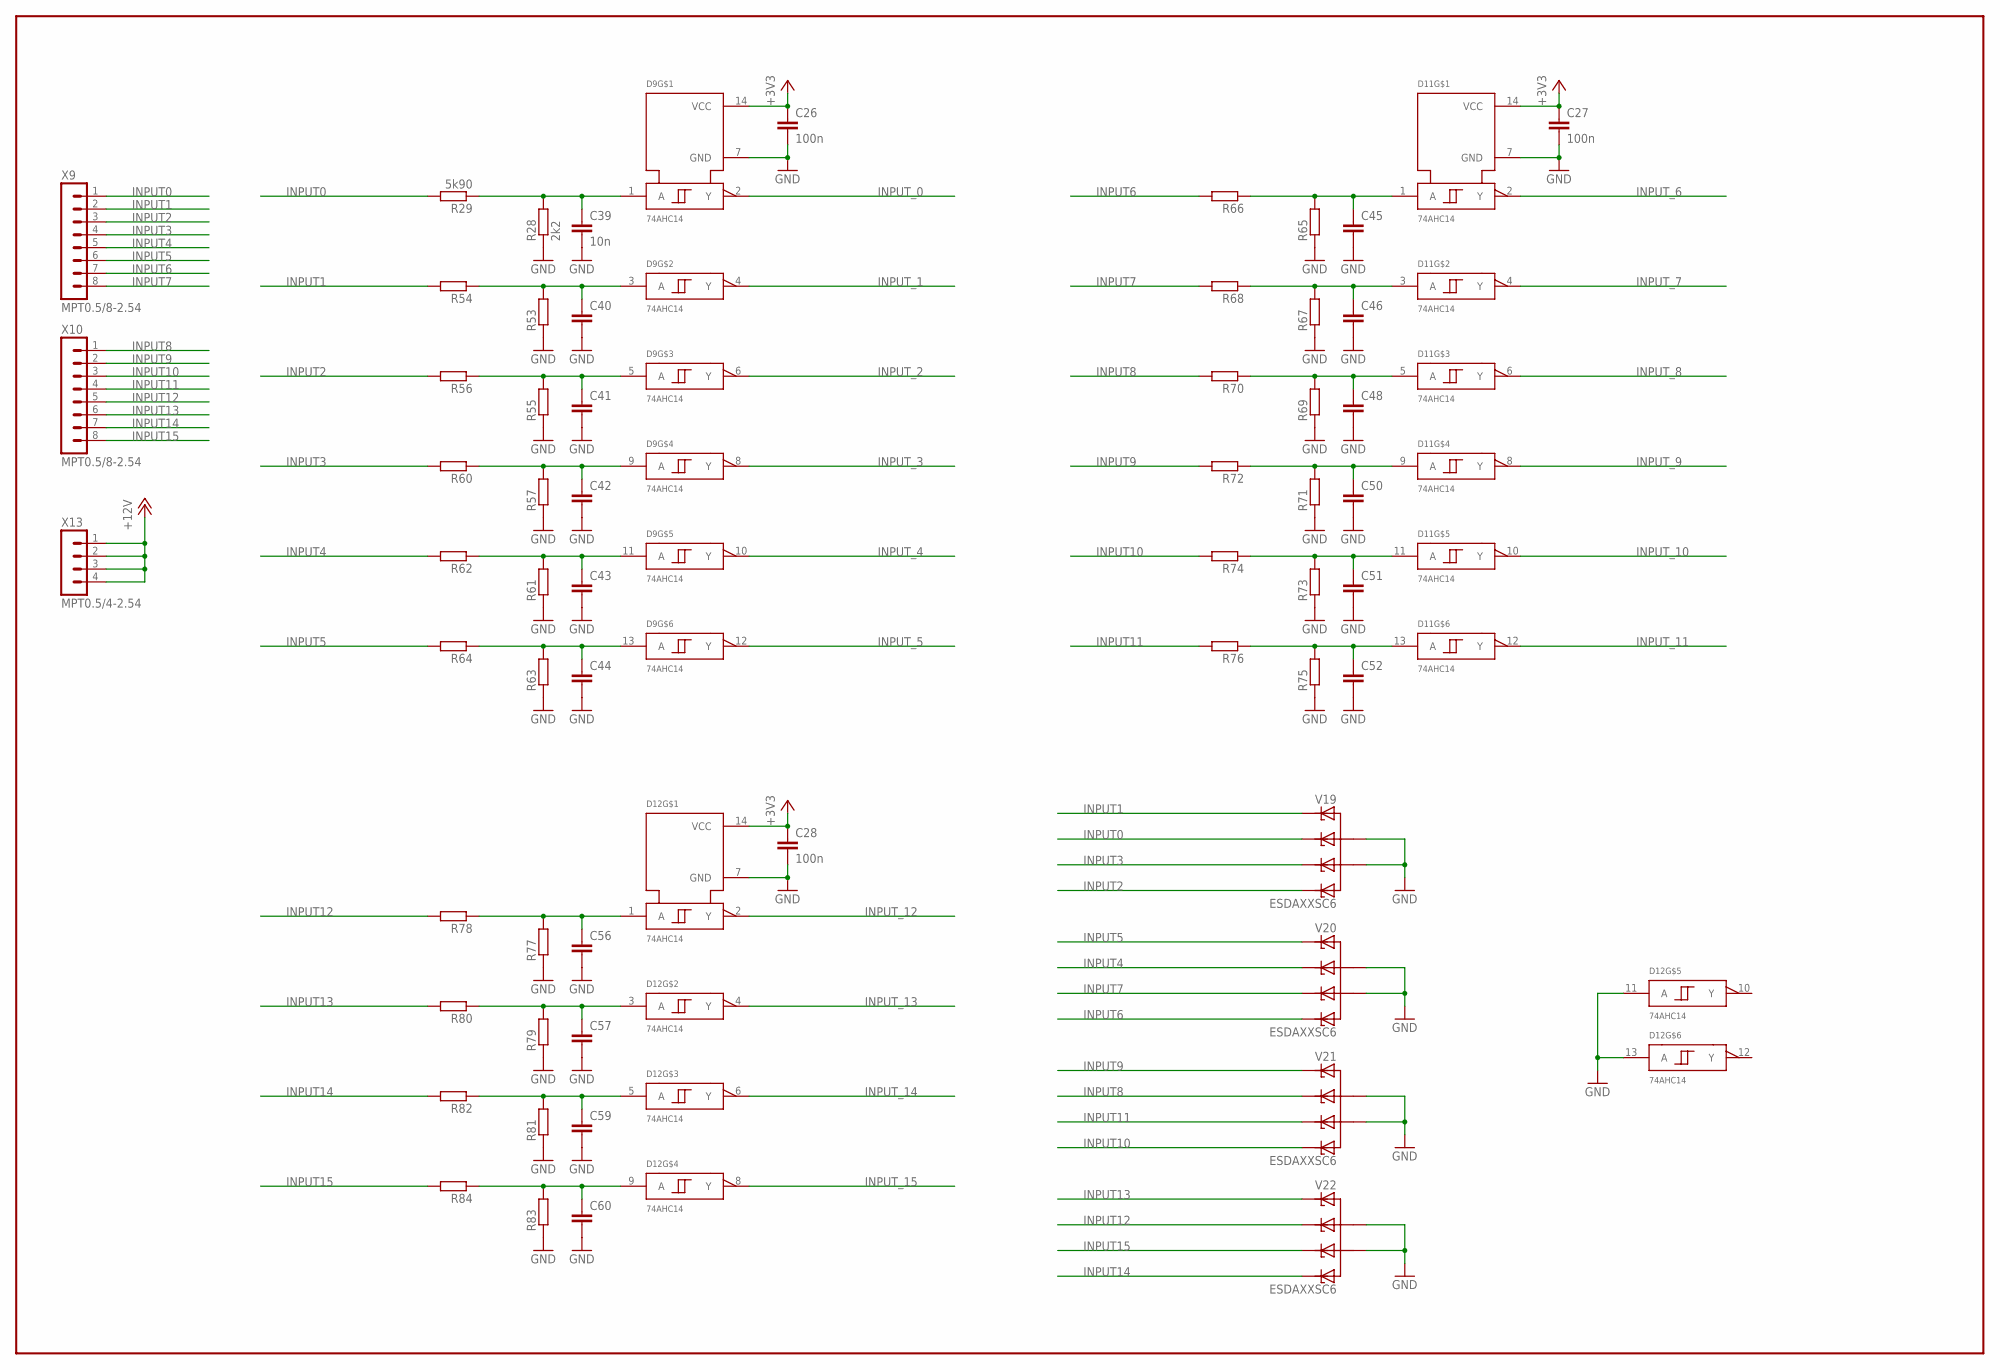
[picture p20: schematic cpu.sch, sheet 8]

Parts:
C26, C27, C28: 100n; C0603
C39: 10n; OMAT_IC_2_C0603
C40, C41, C42, C43, C44, C45, C46, C48, C50, C51, C52, C56, C57, C59, C60: CAP0603; OMAT_IC_2_C0603
D9, D11, D12: 74AHC14; SO14
R28: 2k2; OMAT_IC_2_R0603
R29: 5k90; OMAT_IC_2_R0603
R53, R54, R55, R56, R57, R60, R61, R62, R63, R64, R65, R66, R67, R68, R69, R70, R71, R72, R73, R74, R75, R76, R77, R78, R79, R80, R81, R82, R83, R84: RES0603; OMAT_IC_2_R0603
V19, V20, V21, V22: ESDAXXSC6; OMAT_IC_2_SOT23-6
X9, X10: MPT0.5/8-2.54; OMAT_IC_2_MPT0.5/8-2.54
X13: MPT0.5/4-2.54

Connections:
+3V3: C26.1, C27.1, C28.1, D9.14 (VCC), D11.14 (VCC), D12.14 (VCC); also elsewhere on the board
+12V: X13.1, X13.2, X13.3, X13.4; also elsewhere on the board
GND: C26.2, C27.2, C28.2, C39.2, C40.2, C41.2, C42.2, C43.2, C44.2, C45.2, C46.2, C48.2, C50.2, C51.2, C52.2, C56.2, C57.2, C59.2, C60.2, D9.7 (GND), D11.7 (GND), D12.7 (GND), D12.11 (A), D12.13 (A), R28.1, R53.1, R55.1, R57.1, R61.1, R63.1, R65.1, R67.1, R69.1, R71.1, R73.1, R75.1, R77.1, R79.1, R81.1, R83.1, V19.2 (A), V19.5 (A1), V20.2 (A), V20.5 (A1), V21.2 (A), V21.5 (A1), V22.2 (A), V22.5 (A1); also elsewhere on the board
INPUT0: R29.2, V19.3 (C1), X9.1
INPUT1: R54.2, V19.1 (C), X9.2
INPUT2: R56.2, V19.6 (C3), X9.3
INPUT3: R60.2, V19.4 (C2), X9.4
INPUT4: R62.2, V20.3 (C1), X9.5
INPUT5: R64.2, V20.1 (C), X9.6
INPUT6: R66.2, V20.6 (C3), X9.7
INPUT7: R68.2, V20.4 (C2), X9.8
INPUT8: R70.2, V21.3 (C1), X10.1
INPUT9: R72.2, V21.1 (C), X10.2
INPUT10: R74.2, V21.6 (C3), X10.3
INPUT11: R76.2, V21.4 (C2), X10.4
INPUT12: R78.2, V22.3 (C1), X10.5
INPUT13: R80.2, V22.1 (C), X10.6
INPUT14: R82.2, V22.6 (C3), X10.7
INPUT15: R84.2, V22.4 (C2), X10.8
INPUT_0: D9.2 (Y); also elsewhere on the board
INPUT_1: D9.4 (Y); also elsewhere on the board
INPUT_2: D9.6 (Y); also elsewhere on the board
INPUT_3: D9.8 (Y); also elsewhere on the board
INPUT_4: D9.10 (Y); also elsewhere on the board
INPUT_5: D9.12 (Y); also elsewhere on the board
INPUT_6: D11.2 (Y); also elsewhere on the board
INPUT_7: D11.4 (Y); also elsewhere on the board
INPUT_8: D11.6 (Y); also elsewhere on the board
INPUT_9: D11.8 (Y); also elsewhere on the board
INPUT_10: D11.10 (Y); also elsewhere on the board
INPUT_11: D11.12 (Y); also elsewhere on the board
INPUT_12: D12.2 (Y); also elsewhere on the board
INPUT_13: D12.4 (Y); also elsewhere on the board
INPUT_14: D12.6 (Y); also elsewhere on the board
INPUT_15: D12.8 (Y); also elsewhere on the board
unnamed: C39.1, D9.1 (A), R28.2, R29.1
unnamed: C40.1, D9.3 (A), R53.2, R54.1
unnamed: C41.1, D9.5 (A), R55.2, R56.1
unnamed: C42.1, D9.9 (A), R57.2, R60.1
unnamed: C43.1, D9.11 (A), R61.2, R62.1
unnamed: C44.1, D9.13 (A), R63.2, R64.1
unnamed: C45.1, D11.1 (A), R65.2, R66.1
unnamed: C46.1, D11.3 (A), R67.2, R68.1
unnamed: C48.1, D11.5 (A), R69.2, R70.1
unnamed: C50.1, D11.9 (A), R71.2, R72.1
unnamed: C51.1, D11.11 (A), R73.2, R74.1
unnamed: C52.1, D11.13 (A), R75.2, R76.1
unnamed: C56.1, D12.1 (A), R77.2, R78.1
unnamed: C57.1, D12.3 (A), R79.2, R80.1
unnamed: C59.1, D12.5 (A), R81.2, R82.1
unnamed: C60.1, D12.9 (A), R83.2, R84.1

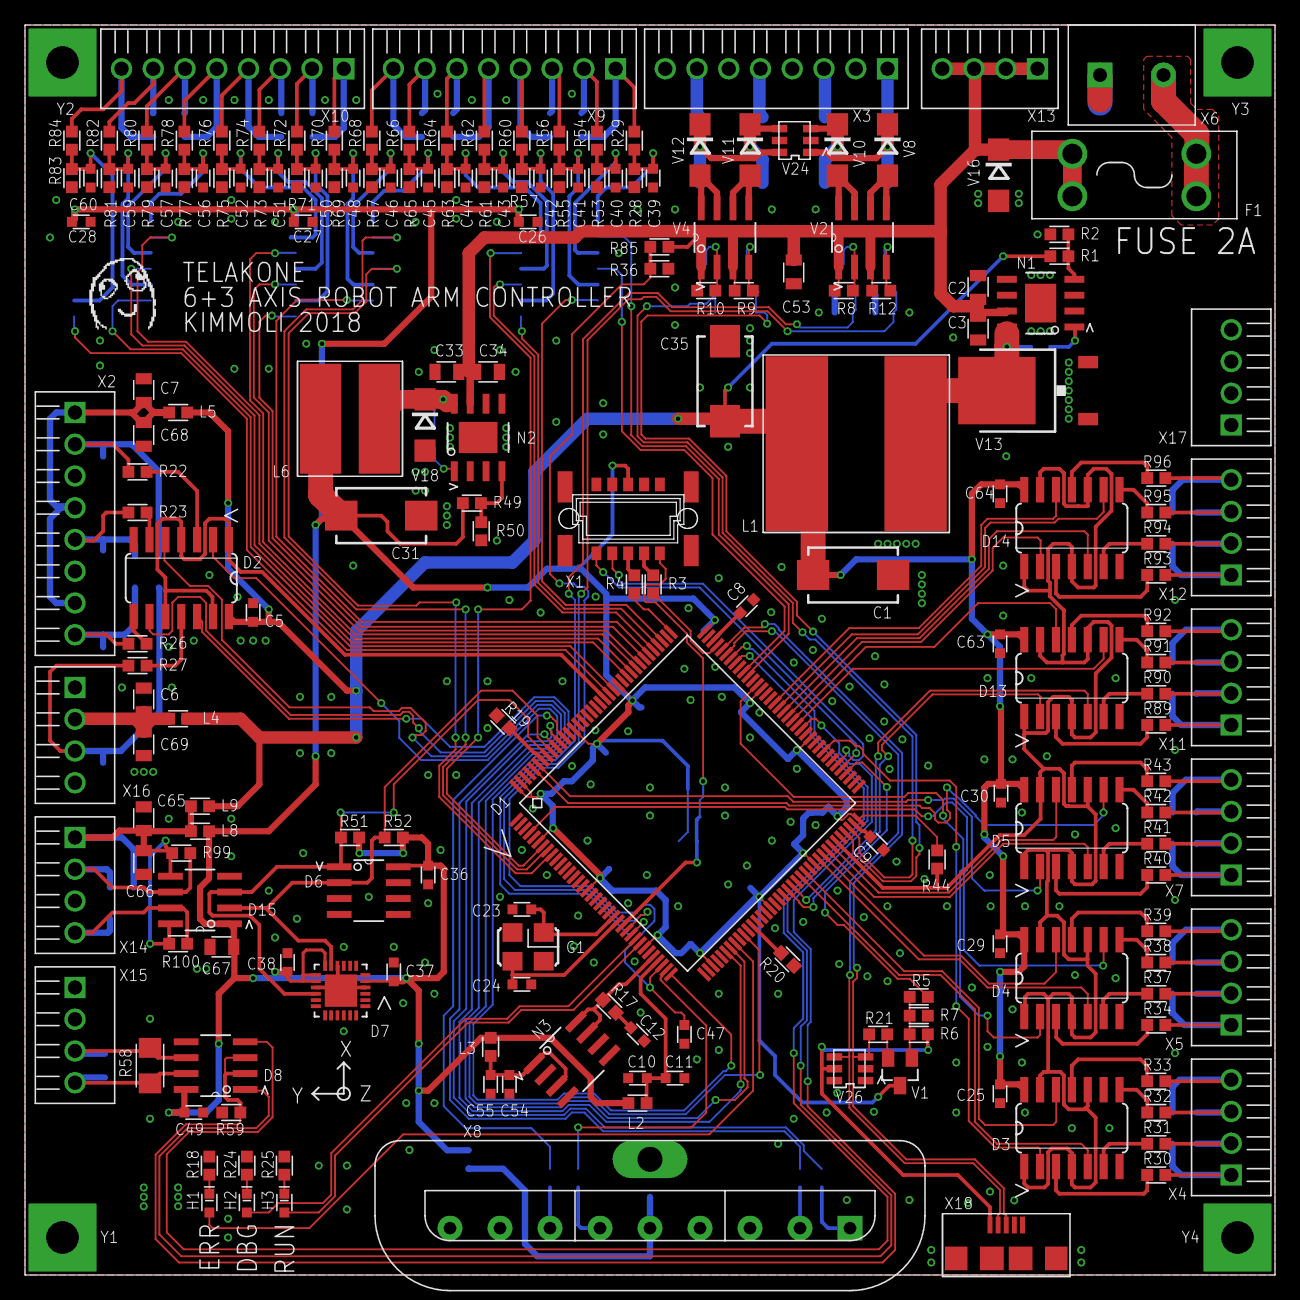
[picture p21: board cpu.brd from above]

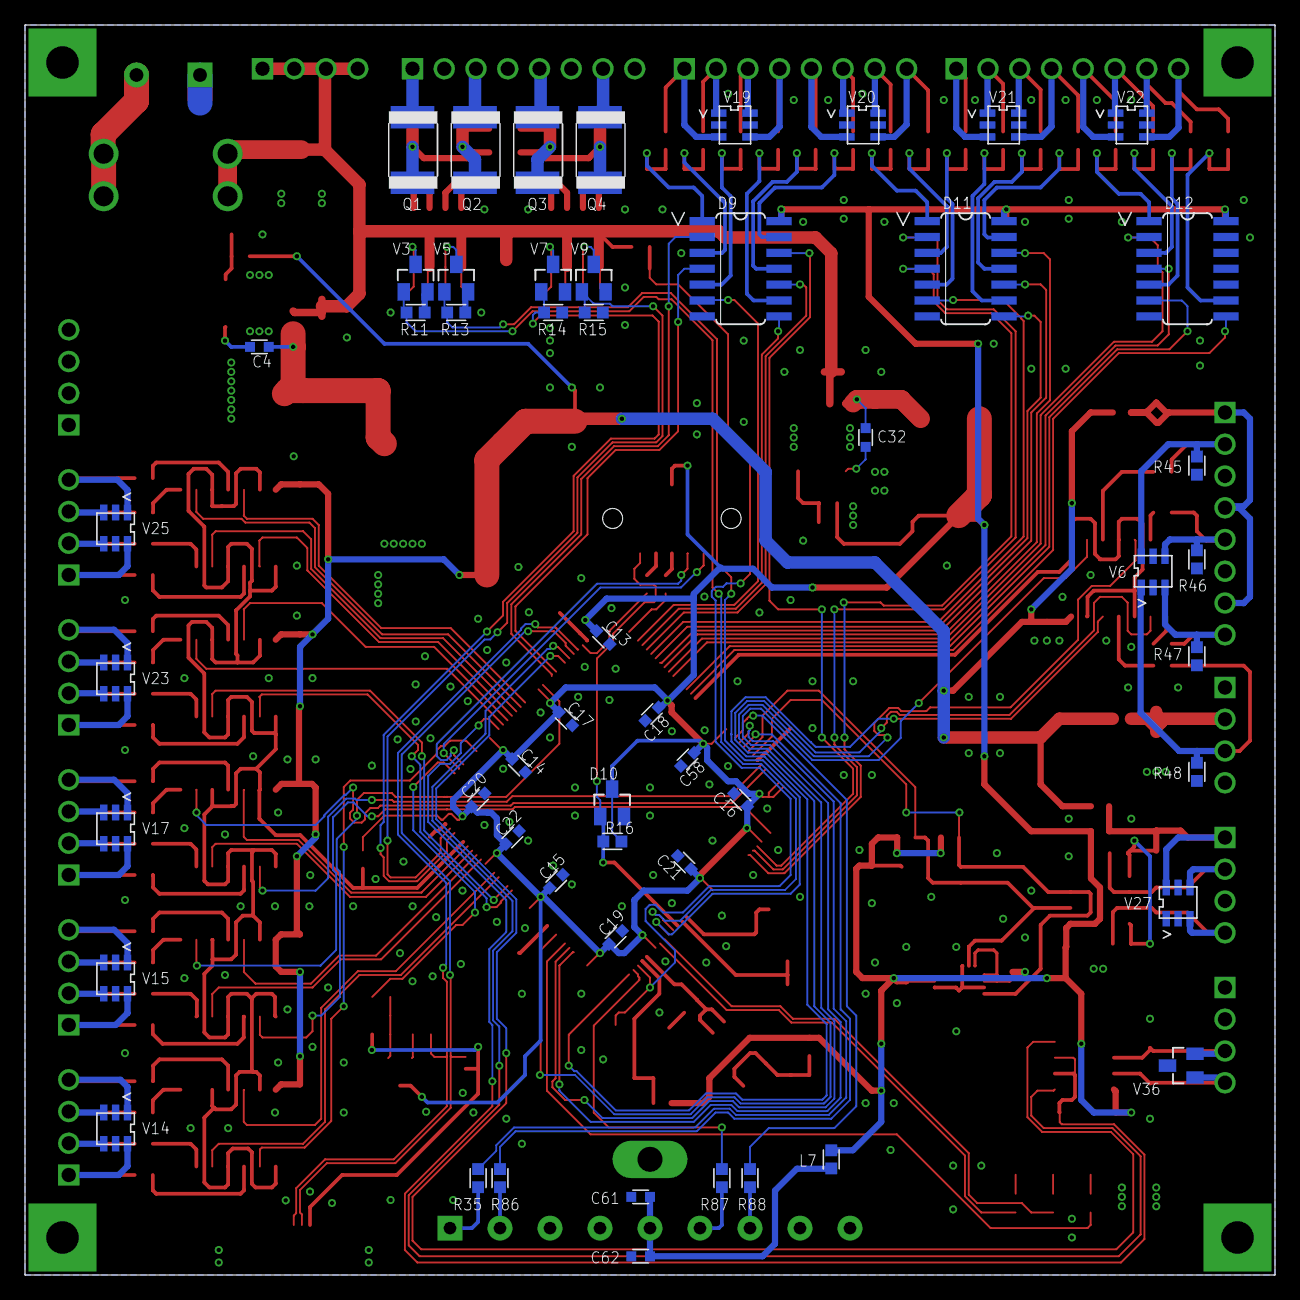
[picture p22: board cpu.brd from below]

Board: 2 copper layers, 100.0 x 100.0 mm, 254 parts (53 on the bottom side), 203 nets.

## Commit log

2018-01-21 debug led
2018-10-22 Add leds, usb renum, gpio directions
2018-10-25 Add iomap, busconts
    [iomap.tsv]
2018-12-10 input liittimet, ena outputit
    [cpu.brd, cpu.sch]
2018-12-11 i2c expander yms
    [cpu.brd, cpu.sch]
2018-12-11 finish schematics, rough initial placement
    [cpu.brd, cpu.sch]
2018-12-12 signals routed, almost
    [cpu.brd, cpu.sch]
2018-12-15 Final v1
    [cpu.brd, cpu.sch]
2018-12-15 Gerber output, pdf
